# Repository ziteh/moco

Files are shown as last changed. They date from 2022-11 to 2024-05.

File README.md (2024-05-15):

# moco

|  SC1  | RD501 |
| :---: | :---: |
|  |  |

BLDC/PMSM motor controller/driver boards. [SC1 Demo video](https://youtu.be/PZ3AqAKdYeg)

- [SC1](/hardware/moco-sc1/): STSPIN32G4 + CSD88584Q5DC. Square PCB 40x40mm.
- [RD501](/hardware/moco-rd501/): DRV8301 + STM32G431. Square PCB 50x50mm.
- [RD321](/hardware/moco-rd321/): STSPIN32F0A + SiZ250DT. Square PCB 32x32mm.
- [OD501](/hardware/moco-od501/): DRV8323H + STM32G431. Round PCB Ø50mm.
- [OI401](/hardware/moco-oi401/): DRV8316C + STM32G431. Round PCB Ø40mm.
- [PG4](/hardware/moco-pg4/):  :construction: WIP.
- [BKD8316](/hardware/moco-bkd8316/): DRV8316 Breakout board

## Disclaimer & License

> [!WARNING]  
> None of the boards here are guaranteed to work.

These files are provided AS IS, without warranty of any kind.  
Including but not limited to manufacturing, assembly, procurement and use at your own risk.  
It is recommended to check yourself before use.  

For the full statement, please see license.  
Hardware licensed under the [CERN-OHL-P v2](/LICENSE-CERN-OHL-P), firmware licensed under the [MIT License](/LICENSE-MIT).

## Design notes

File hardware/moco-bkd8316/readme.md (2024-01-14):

# moco-bkd8316

- [DRV8316](https://www.ti.com/product/DRV8316) 40V max 8A peak, gate driver + FETs power stage + current sensing.

## PCB

### Board Characteristics

- Copper layer count: 2
- Board overall dimensions: 35.5 x 41 mm
- Min track/spacing: 0.2 mm / 0.2 mm
- Min hole diameter: 0.3 mm
- Castellated pads: No
- Edge card connectors: No
- Plated board edge: No

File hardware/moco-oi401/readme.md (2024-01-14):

# moco-OI401

- 10V~35V operating voltage
- 8A peak current
- 3x or 6xPWM control
- 3-Phase low-side current sense
- Ø40mm round PCB
- 3xM2 mounting holes, P.C.D Ø35.5mm
- [STM32G431CBU6](https://www.st.com/en/microcontrollers-microprocessors/stm32g431cb.html) 170 MHz MCU
- [DRV8316C](https://www.ti.com/product/DRV8316C) gate driver integrated FETs
- AS5047x magnetic encoder

## Pinmap

| Description | DRV8316 | STM32 | STM32 Func |
| --- | --- | ----- | --- |
| PWM-A High | INHA | PA10  | TIM1_CH3 |
| PWM-B High | INHB | PA9 | TIM1_CH2 |
| PWM-C High | INHC | PA8 | TIM1_CH1 |
| PWM-A Low | INLA | PC15  | TIM1_CH3N  |
| PWM-B Low | INLB | PA12  | TIM1_CH2N  |
| PWM-C Low | INLC | PB13  | TIM1_CH1N  |
| Current sense A | SOA | PA5 | ADC2_IN13  |
| Current sense B | SOB | PA6 | ADC2_IN3 |
| Current sense C | SOC | PA7 | ADC2_IN4 |
| nEnable | DRVOFF  | PB12  | |
| nFAULT | nFAULT  | PB11  | |
| SPI SCLK | SCLK | PB3 | SPI1 |
| SPI MISO | SDI | PB4 | SPI1 |
| SPI MOSI | SDO | PB5 | SPI1 |
| SPI nCS DRV8316 | nSCS | PB9 | |
| SPI nCS AS5047x | -- | PB2 | |
| USART Tx | -- | PA2 | USART2 |
| USART Rx | -- | PA3 | USART2 |
| User LED 1 (Red) | -- | PA0 | Active LOW |
| User LED 2 (Blue) | -- | PA1 | Active LOW |
| 5V indicator LED (Green) | -- | -- | |

## Jumper
- SB1 (3.3V LDO Bypass)
  - ON: 3.3V LDO bypassed, 3.3V provided through the buck regulator of DRV8316.
  - OFF (Default): 3.3V provided through the LDO.
- SB2 (nSLEEP Reset)
  - ON: Connected DRV8316 `nSLEEP` pin to RESET button.
  - OFF (Default): Disconnected DRV8316 `nSLEEP` pin to RESET button.
- SB3 (Voltage Reference Selection)
  - ON (Default): Connected +3.3V to STM32 `VREF+` and DRV8316 `VREF/LILM`, `VREF+` used as input.
  - OFF: Disconnected +3.3V to STM32 `VREF+` and DRV8316 `VREF/LILM`, voltage reference powered by STM32G4 embed voltage reference buffer, `VREF+` used as output.

## SPI

- Mode=1
  - CPOL=0. Clock is low when idle.
  - CPHA=1. Data sampled on 2nd edge (i.e. falling edge).
- 16-bit data frame.
- MSB first.
- nCS pin active low.
- 5MHz clock (limited by DRV8316).

## Board Characteristics

- Copper layer count: 2
- Board overall dimensions: 40 x 40 mm
- Min track/spacing: 0.13 mm / 0.13 mm
- Min hole diameter: 0.3 mm
- Castellated pads: No
- Edge card connectors: No
- Plated board edge: No

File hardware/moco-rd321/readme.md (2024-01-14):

# moco-RD321

- 6.7V~35V, 12A
- 3-Phase low-side current sensing. OP-Amp Gain=6.74, Shunt resistor=20mΩ
- Overcurrent detection. Ith=30A @ OC_COMPth=500mV
- Input voltage sensing
- 32x32mm square PCB, 4xM2 mounting holes
- [STSPIN32F0A](https://www.st.com/en/motor-drivers/stspin32f0a.html) 3-phase gate driver with embdded MCU SiP
  - STM32F031C6 48MHz, 4KB SRAM, 32KB Flash
  - 600mA sink/source gate drivers, integrated bootstrap diodes
  - 12V LDO and 3.3V buck
- [SiZ250DT](https://www.vishay.com/en/product/77227/) Dual N-MOSFET, 60V, 38A, 3.3x3.3mm
- MA702 magnetic encoder, SPI
- 2x04 2.54mm Pin header for debug, JST SM03B-SRSS-TB 1x03 for Serial and I2C

## Pinmap

| Description | Analog IC | STM32 | STM32 Func |
| --- | --- | ----- | --- |
| High-side U | HS1 | PA8 | TIM1_CH1 |
| High-side V | HS2 | PA9 | TIM1_CH2 |
| High-side W | HS3 | PA10  | TIM1_CH3 |
| Low-side U | LS1 | PB13  | TIM1_CH1N |
| Low-side V | LS2 | PB14  | TIM1_CH2N |
| Low-side W | LS3 | PB15  | TIM1_CH3N |
| OC threshold select 1 | OC_TH_STBY1  | PF7 | Push-pull output |
| OC threshold select 2 | OC_TH_STBY2  | PF6 | Push-pull output |
| OC protection selection  | OC_SEL | PA11  | Push-pull output |
| OC comparator output | OC_COMP_INT  | PB12  | TIM1_BKIN |
| OC comparator output | OC_COMP_INT2 | PA12  | TIM1_ETR |
| Current sense U | OP3O | PA0 | ADC_IN0 |
| Current sense V | OP2O | PA1 | ADC_IN1 |
| Current sense W | OP1O | PB1 | ADC_IN9 |
| VM sense | -- | PA4 | ADC_IN4 |
| SPI SCLK | -- | PA5 | SPI1 |
| SPI MISO | -- | PA6 | SPI1 |
| SPI MOSI | -- | PA7 | SPI1 |
| SPI nCS MA702 | -- | PA15  | |
| USART Tx | -- | PA2 | USART1 |
| USART Rx | -- | PA3 | USART1 |
| I2C SCL | -- | PB6 | I2C1 |
| I2C SDA | -- | PB7 | I2C1 |
| SWDIO | -- | PA13  | |
| SWCLK | -- | PA14  | |
| Connected to GND | -- | BOOT0 | |
| User LED (Red) | -- | PF0 | Active HIGH |
| 12V indicator LED (Blue) | -- | -- | |

> - Unused GPIOs inside the package should be config to output low: PB0, PB2, PB3, PB4, PB5, PB8, PB9, PB10, PB11, PC13, PC14, PC15.
> - OC_TH_STBY1 and OC_TH_STBY2 should be HIGH for 500mV OC threshold.
> - For analog IC, the GPIO input config without pull-up or -down is always allowed.

## PCB

### Jumper

If input voltage (i.e. VM)<15V then close `SB1` to connect VM pin and VREG12 pin.

### Board Characteristics

- Copper layer count: 4
- Board overall dimensions: 32 x 32 mm
- Min track/spacing: 0.13 mm / 0.13 mm
- Min hole diameter: 0.3 mm
- Castellated pads: No
- Edge card connectors: No
- Plated board edge: No
- 1oz copper

## SPI

MA702 encoder SPI:
- Mode:
  - 0 (CPOL=0, CPHA=0) or 1 (CPOL=1, CPHA=1)
  - Data sampled on first edge
- 16-bit data frame
- MSB first
- nCS pin active low
- 25MHz clock

## MCU

| STSPIN32*x* | [F0](https://www.st.com/en/motor-drivers/stspin32f0.html) | [F0***A***](https://www.st.com/en/motor-drivers/stspin32f0a.html) | [F0***B***](https://www.st.com/en/motor-drivers/stspin32f0b.html) |
| --- | --- | --- | --- |
| Operating voltage | 8~45V | 6.7~45V | 6.7~45V |
| OP-Amps | 4 | 3 | 1 |
| GPIOs | 15 | 16 | 20 |
| BOOT0 pin | -- | Yes | Yes |
| 3FG decoding logic for Hall sensors | Yes | -- | -- |
| Comparator | OCP | OCP and current control | OCP and current control |
| Package | QFN 7x7mm 1EP | QFN 7x7mm 1EP | QFN 7x7mm 1EP |

> [Solved: STSPIN32F0 vs STSPIN32F0A vs STSPIN32F0B - STMicroelectronics Community](https://community.st.com/t5/power-management/stspin32f0-vs-stspin32f0a-vs-stspin32f0b/td-p/273388)

## Reference

- [qwertpas/O32controller: Miniature closed-loop controller for brushless DC motors](https://github.com/qwertpas/O32controller)
- [STspin32G4 support - hardware support - SimpleFOC Community](https://community.simplefoc.com/t/stspin32g4-support/2027/6?page=3)
- ST AN5397 *"Current Sensing in motion control applications"*
- ST AN4999 *"STSPIN32F0/F0A/F0B overcurrent protection"*
- ST DB3364 *"STEVAL-SPIN3202: STSPIN32F0A advanced 3-phase BLDC driver with embedded STM32 MCU single shunt evaluation board"*
- ST DB4049 *"EVALKIT-ROBOT-1: Compact reference design kit for robotics and automation based on STSPIN32F0A"*
- ST DB3798 *"STEVAL-ESC002V1: Electronic Speed Controller reference design based on STSPIN32F0A"*
- TI SLUA887 *"Bootstrap Circuitry Selection for Half-Bridge Configurations"*
- Diodes DN1156 *"Gate Drivers in BLDC Motors"*

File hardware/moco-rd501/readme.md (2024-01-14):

# moco-RD501



STM32G431C8T6 MCU, DRV8301 gate driver, CSD18540Q5B power N-MOSFETs and AS5047x magnetic encoder.

Based on [ODrive](https://github.com/odriverobotics/ODriveHardware) `v3.5` PCB and [SimpleFOC](https://simplefoc.com/) firmware.

> Seems unstable.

| Front | Back | Layers |
| --- | --- | --- |
|  |  |  |

### Pinmap

| Description | STM32 Pin |
| --- | --- |
| PWM-A High | PA8 |
| PWM-B High | PA9 |
| PWM-C High | PA10 |
| PWM-A Low | PC13 |
| PWM-B Low | PA12 |
| PWM-C Low | PB15 |
| EN_Gate (Enable) | PB3 |
| nFAULT | PB10 |
| Encoder A | PB5 |
| Encoder B | PB6 |
| Encoder I | PB4 |
| SPI SCLK | PA5 |
| SPI MISO | PA6 |
| SPI MOSI | PA7 |
| SPI nCS DRV8301 | PB13 |
| SPI nCS AS5047x | PB14 |
| SPI nCS CAN-Bus | PB9 |
| CAN-Bus INT | PA11 |
| USART Tx | PA2 |
| USART Rx | PA3 |
| I2C SCL | PA15 |
| I2C SDA | PB7 |
| Current sense 1 (CH-B) | PA0 |
| Current sense 2 (CH-C) | PA1 |
| Temperature sense | PA4 |
| V_drive sense | PB12 |
| User LED 1 (Red) | PB0 |
| User LED 2 (Blue) | PB1 |
| GPIO PB2 | PB2 |
| GPIO PB11 | PB11 |

### Board Characteristics

- Copper layer count: 4
- Board overall dimensions: 50 x 50 mm
- Min track/spacing: 0.2 mm / 0.2 mm
- Min hole diameter: 0.2 mm
- Castellated pads: No
- Edge card connectors: No
- Plated board edge: No

Support JLCPCB's PCBA service.

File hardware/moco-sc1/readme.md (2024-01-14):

# moco-SC1

- 10V~35V, 12A
- 3-Phase low-side current sensing. Op-amp Gain=6.74, shunt resistor=20mΩ
- Input voltage sensing
- 40x40mm square PCB, 4xM3 mounting holes.
- [STSPIN32G4](https://www.st.com/en/motor-drivers/stspin32g4.html) 3-phase gate driver with embdded MCU SiP
  - [STM32G431VBx3](https://www.st.com/en/microcontrollers-microprocessors/stm32g431vb.html) 170MHz, 32KB SRAM, 128KB Flash
  - 1A sink/source gate drivers, integrated bootstrap diodes
  - 8~15V/200mA programmable buck for gate driver and 3.3V/150mA LDO
- [CSD88584Q5DC](https://www.ti.com/product/CSD88584Q5DC) Dual N-MOSFET half-bridge, 40V, 50A, 5x6mm
- [MA702](https://www.monolithicpower.com/en/ma702.html) magnetic encoder, SPI interface
- [TCAN33x](https://www.ti.com/product/TCAN330) 3.3V CAN transceiver
- 2x04 2.54mm Pin header for debug, JST GH 1.25mm 1x03 for CAN bus

## PCB

PCB online preview available [here](https://kicanvas.org/?github=https%3A%2F%2Fgithub.com%2Fziteh%2Fmoco%2Ftree%2Fmain%2Fhardware%2Fmoco-sc1), powered by [KiCanvas](https://github.com/theacodes/kicanvas).

### Jumper

`SB1`: Close to connect CAN bus 120Ω terminal resistor.

### Board Characteristics

- Copper layer count: 4
- Board overall dimensions: 40 x 40 mm
- Min track/spacing: 0.2 mm / 0.2 mm
- Min hole diameter: 0.3 mm
- Castellated pads: No
- Edge card connectors: No
- Plated board edge: No
- 1 or 2oz copper available

## SPI

MA702 encoder SPI:
- Mode:
  - 0 (CPOL=0, CPHA=0) or 3 (CPOL=1, CPHA=1) detected automatically
  - Data sampled on rising edge, transmission on falling
- 16-bit data frame
- MSB first
- nCS pin active low
- 25MHz clock max

## Pinmap

| Description | Gate Driver | STM32 | STM32 Func |
| --- | --- | ----- | --- |
| High-side A | INH1 | PE9 | TIM1_CH1 |
| High-side B | INH2 | PE11  | TIM1_CH2 |
| High-side C | INH3 | PE13  | TIM1_CH3 |
| Low-side A | INL1 | PE8 | TIM1_CH1N |
| Low-side B | INL2 | PE10  | TIM1_CH2N |
| Low-side C | INL3 | PE12  | TIM1_CH3N |
| Active high for wakeup | WAKE | PE7 | Push-pull output |
| Device ready signal | READY | PE14  | TIM1_BKIN2, pull-up input |
| Fault signal | NFAULT | PE15  | TIM1_BKIN, pull-up input  |
| | SCL | PC8 | I2C3 |
| | SDA | PC9 | I2C3 |
| Enable short-circuit protection | SCREF | -- | |
| Current sense Op-amp In+ A | -- | PA1 | OPAMP1_VINP |
| Current sense Op-amp In- A | -- | PA3 | OPAMP1_VINM |
| Current sense Op-amp Out A | -- | PA2 | OPAMP1_VOUT, ADC1_IN3 |
| Current sense Op-amp In+ B | -- | PA7 | OPAMP2_VINP |
| Current sense Op-amp In- B | -- | PC5 | OPAMP2_VINM |
| Current sense Op-amp Out B | -- | PA6 | OPAMP2_VOUT, ADC2_IN3 |
| Current sense Op-amp In+ C | -- | PB0 | OPAMP3_VINP |
| Current sense Op-amp In- C | -- | PB2 | OPAMP3_VINM |
| Current sense Op-amp Out C | -- | PB1 | OPAMP3_VOUT, ADC1_IN12 |
| VBUS sense | -- | PA4 | ADC2_IN17 |
| SPI SCLK | -- | PB3 | SPI1/3 |
| SPI MISO | -- | PB4 | SPI1/3 |
| SPI MOSI | -- | PB5 | SPI1/3 |
| SPI nCS MA702 | -- | PB6 | |
| USART TX | -- | PA9 | USART1 |
| USART RX | -- | PA10  | USART1 |
| CAN TX | -- | PA12  | FDCAN1 |
| CAN RX | -- | PA11  | FDCAN1 |
| SWDIO | -- | PA13  | |
| SWCLK | -- | PA14  | |
| SWO | -- | PA15  | |
| HSE OSC | -- | PF0 | OSC_IN |
| HSE OSC | -- | PF1 | OSC_OUT |
| Reset | -- | PG10  | NRST |
| BOOT, connected to GND | -- | PB8 | BOOT0 |
| User LED (Red), active high | -- | PA0 | TIM2_CH1 |
| VCC indicator LED (Blue) | -- | -- | |

> - For gate driver internal connected GPIO, the input pin config without pull-up or -down is always allowed.
> - It is recommended to set PB8 (BOOT0) in a mode other than analog mode after startup to limit consumption.

## STSPIN32 SiP

| STSPIN32 | [F0][32f0] | [F0A][32f0a] | [F0B][32f0b] | [G4][32g4] |
| --- | --- | --- | --- | --- |
| MCU | STM32F031C6 | STM32F031C6 | STM32F031C6 | STM32G431VB |
| Clock | 48 MHz | 48 MHz | 48 MHz | 170 MHz |
| SRAM | 4 KB | 4 KB | 4 KB | 32 KB |
| Flash | 32 KB | 32 KB | 32 KB | 128 KB |
| Operating voltage | 8~45V | 6.7~45V | 6.7~45V | 5.5~75V |
| OP-Amps | 4 | 3 | 1 | 3 |
| GPIOs | 15 | 16 | 20 | 40 |
| CAN Bus | 0 | 0 | 0 | 1 (CAN-FD) |
| USB | 0 | 0 | 0 | 1 (USB 2.0 FS) |
| BOOT0 pin | -- | Yes | Yes | Yes |
| Package | QFN-48 7x7mm 1EP | QFN-48 7x7mm 1EP | QFN-48 7x7mm 1EP | QFN-64 9x9mm 1EP |

> [Solved: STSPIN32F0 vs STSPIN32F0A vs STSPIN32F0B - STMicroelectronics Community](https://community.st.com/t5/power-management/stspin32f0-vs-stspin32f0a-vs-stspin32f0b/td-p/273388)

[32f0]: https://www.st.com/en/motor-drivers/stspin32f0.html
[32f0a]: https://www.st.com/en/motor-drivers/stspin32f0a.html
[32f0b]: https://www.st.com/en/motor-drivers/stspin32f0b.html
[32g4]: https://www.st.com/en/motor-drivers/stspin32g4.html

## Reference

- [runger1101001/simplefoc_funqi_example: Sample firmware for STSPIN32G4 based BLDC driver](https://github.com/runger1101001/simplefoc_funqi_example)
- [qwertpas/O32controller: Miniature closed-loop controller for brushless DC motors](https://github.com/qwertpas/O32controller)
- [Juanduino/STSPIN32G4-FunQi-Stack: SimpleFoc Format Dev. for potential 8pin PWM stepper use w. 4th half-bridge (also 6pin PWM BLDC use w. extra FET driver for eg. brake-resistor)](https://github.com/Juanduino/STSPIN32G4-FunQi-Stack)
  - [STspin32G4 support - hardware support - SimpleFOC Community](https://community.simplefoc.com/t/stspin32g4-support/2027/6?page=3)
- [EVSPIN32G4 - STSPIN32G4 demonstration board for three-phase brushless motors - STMicroelectronics](https://www.st.com/en/evaluation-tools/evspin32g4.html)
- [TIDA-01516 reference design | TI.com](https://www.ti.com/tool/TIDA-01516)
- [TIDA-00774 reference design | TI.com](https://www.ti.com/tool/TIDA-00774)
- ST AN5397 *"Current Sensing in motion control applications"*
- TI SLUA887 *"Bootstrap Circuitry Selection for Half-Bridge Configurations"*
- Diodes DN1156 *"Gate Drivers in BLDC Motors"*

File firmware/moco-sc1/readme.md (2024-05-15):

# moco SC1 Firmware

Simple firmware for moco SC1.

Currently only open loop velocity control, with SVPWM (Space Vector Pulse Width Modulation) or SPWM (Sinusoidal Pulse Width Modulation).

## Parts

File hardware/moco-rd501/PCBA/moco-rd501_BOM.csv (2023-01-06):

Comment | Designator | Footprint | LCSC
82pF | C5 | C_0402_1005Metric | C107011
47uF/50V | C26 | CP_Elec_6.3x7.7 | C108053
15nF | C8 | C_0402_1005Metric | C114405
1k | R19,R8 | R_0402_1005Metric | C11702
NCP18XH103F03RB | TH1 | R_0603_1608Metric | C13564
16MHz | Y2 | Crystal_SMD_3225-4Pin_3.2x2.5mm | C13738
100nF/50V | C14,C16,C19,C22,C23,C24 | C_0603_1608Metric | C14663
100nF | C36,C39,C40,C41,C42,C44,C45,C46 | C_0402_1005Metric | C1525
22nF | C18 | C_0402_1005Metric | C1532
12pF | C37,C38 | C_0402_1005Metric | C1547
10uF | C2 | C_0402_1005Metric | C15525
22pF | C47,C48 | C_0402_1005Metric | C1555
2.2nF | C20,C21,C6,C7 | C_0603_1608Metric | C1604
MCP25625 | U4 | QFN-28-1EP_6x6mm_P0.65mm_EP4.25x4.25mm | C191253
2.2R | R13,R14,R25,R26,R28,R29 | R_0603_1608Metric | C22939
4.7uF | C3 | C_0402_1005Metric | C23733
120R | R30,R31,R37 | R_0402_1005Metric | C25079
22R | R16,R17 | R_0402_1005Metric | C25092
330R | R9 | R_0402_1005Metric | C25104
680R | R5,R7 | R_0402_1005Metric | C25130
10k | R18,R2,R20,R24,R35,R36,R38,R4,R6 | R_0402_1005Metric | C25744
18k | R23,R33 | R_0402_1005Metric | C25762
220k 1% | R22 | R_0402_1005Metric | C25767
47k | R15 | R_0402_1005Metric | C25792
3.3k | R10,R11,R12,R21,R34 | R_0402_1005Metric | C25890
4.7k | R1,R3 | R_0402_1005Metric | C25900
Conn_02x02_Top_Bottom | J6,J7 | JST_GH_SM03B-GHS-TB_1x03-1MP_P1.25mm_Horizontal | C2829252
Conn_01x06 | J1 | JST_GH_SM06B-GHS-TB_1x06-1MP_P1.25mm_Horizontal | C2829255
Conn_01x09 | J4 | JST_GH_SM09B-GHS-TB_1x09-1MP_P1.25mm_Horizontal | C2829258
4.7uF/50V | C11,C17 | C_1206_3216Metric | C29823
22uH/1.5A | L1 | L_Bourns-SRN8040_8x8.15mm | C354640
LED_BAGR | LD1 | RGB LED 1.6x1.6mm | C375569
0.5mΩ | R27,R32 | R_2512_6332Metric | C469426
AS5147 | U5 | TSSOP-14_4.4x5mm_P0.65mm | C481876
2.2uF/16V | C10,C33 | C_0402_1005Metric | C501836
2.2uF/50V | C15,C27,C9 | C_1206_3216Metric | C50254
SW_Push | SW1,SW2 | SW_SPST_CK_RS282G05A3 | C520860
270pF | C1,C4 | C_0402_1005Metric | C524551
1uF | C12,C13,C43 | C_0402_1005Metric | C52923
STM32G431CBT6 | U3 | LQFP-48_7x7mm_P0.5mm | C529355
8MHz | Y1 | Crystal_SMD_3225-4Pin_3.2x2.5mm | C57131
68uF | C25 | CP_EIA-6032-28_Kemet-C | C7220
CSD18540Q5B | Q1,Q2,Q3,Q4,Q5,Q6 | TDSON-8-1 | C86513
XC6220B331MR | U1 | SOT-23-5 | C86534
SS34 | D1 | D_SMA | C8678
Conn_01x02 | J3 | AMASS_XT60-M_1x02_P7.20mm_Vertical | C98733
DRV8301 | U2 | HTSSOP-56-1EP_6.1x14mm_P0.5mm_EP3.61x6.35mm | C98969
Debug | J2 | PinHeader_1x06_P2.54mm_Vertical
Conn_01x03 | J5 | AMASS MR30PB-F
100nF | C50 | C_0603_1608Metric
22uF/50V | C29 | C_1210_3225Metric_Pad1.33x2.70mm_HandSolder
1uF | C49 | C_0603_1608Metric
22uF/50V | C30 | C_1210_3225Metric_Pad1.33x2.70mm_HandSolder
22uF/50V | C31 | C_1210_3225Metric_Pad1.33x2.70mm_HandSolder
22uF/50V | C32 | C_1210_3225Metric_Pad1.33x2.70mm_HandSolder
22uF/50V | C28 | C_1210_3225Metric_Pad1.33x2.70mm_HandSolder
22uF/50V | C35 | C_1210_3225Metric_Pad1.33x2.70mm_HandSolder
22uF/50V | C34 | C_1210_3225Metric_Pad1.33x2.70mm_HandSolder

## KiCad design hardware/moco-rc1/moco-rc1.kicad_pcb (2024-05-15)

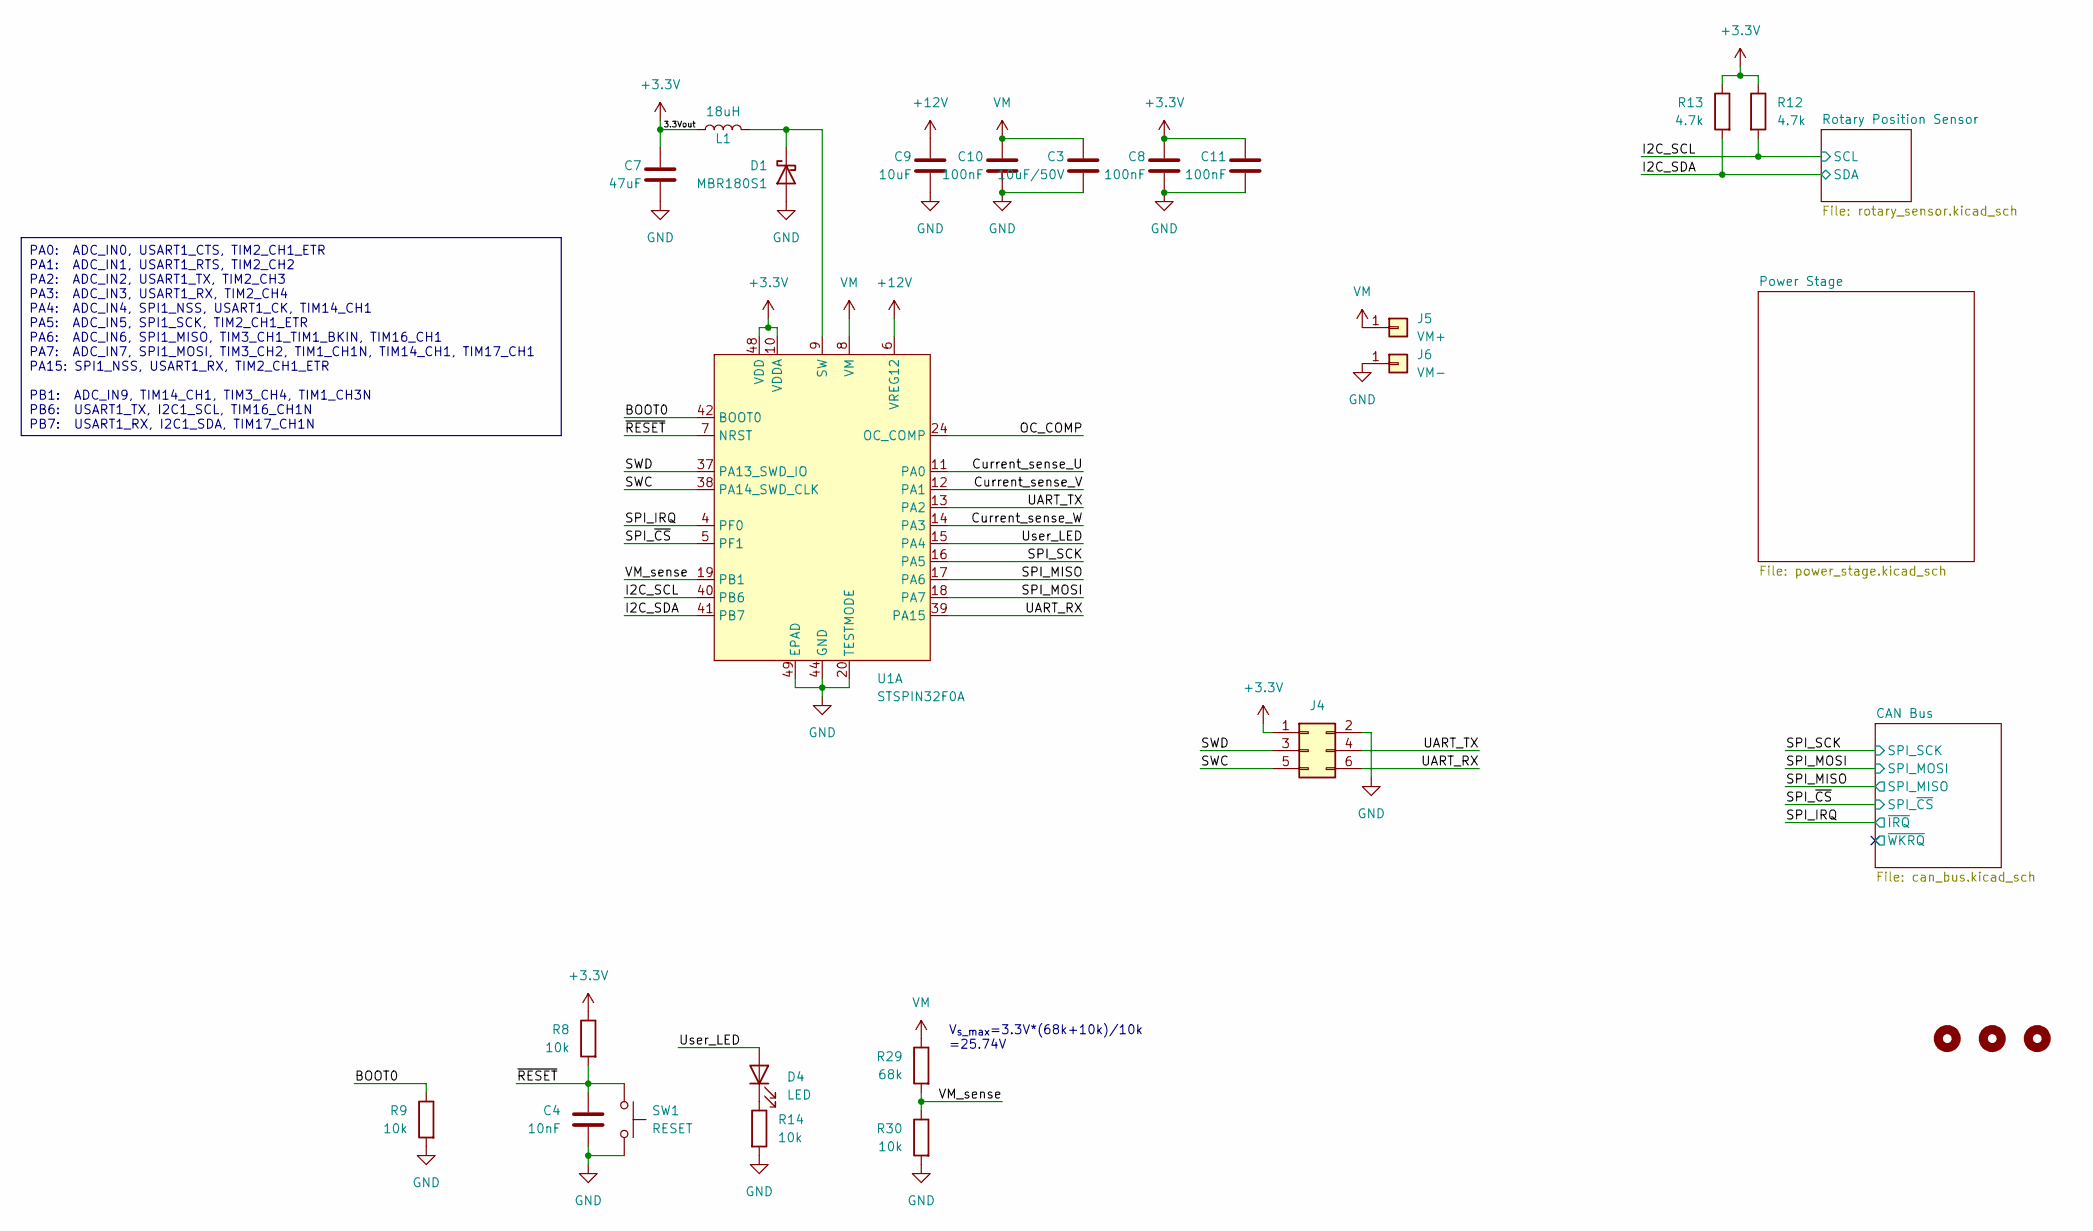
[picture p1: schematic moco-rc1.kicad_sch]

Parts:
C3: 10uF/50V; C_0805_2012Metric; MFR. Part# GRM21BR61H106KE43L; LCSC C440198
C4: 10nF; C_0402_1005Metric
C7: 47uF; C_0805_2012Metric; MFR. Part# GRM21BR61H106KE43L; LCSC C440198
C8, C10, C11: 100nF; C_0402_1005Metric; MFR. Part# GRM21BR61H106KE43L; LCSC C440198
C9: 10uF; C_0402_1005Metric; MFR. Part# GRM21BR61H106KE43L; LCSC C440198
D1: MBR180S1; D_SOD-123F; MFR. Part# MBR180S1-7; LCSC C526660
D4: LED; LED_0603_1608Metric
H1, H2, H3: MountingHole; MountingHole_2.2mm_M2_ISO7380
J4: Conn_02x03_Odd_Even; PinHeader_2x03_P2.54mm_Vertical
J5: VM+; Conn_1x1_3.7_1.5
J6: VM-; Conn_1x1_3.7_1.5
L1: 18uH; L_Neosid_SMS-ME3015; MFR. Part# FNR3012S180MT; LCSC C528020
R8, R9, R14, R30: 10k; R_0402_1005Metric
R12, R13: 4.7k; R_0402_1005Metric
R29: 68k; R_0402_1005Metric
SW1: RESET; SW_SPST_B3U-1000P
U1: STSPIN32F0A; VFQFN-48_7x7_EP2.8mm_Pitch0.5mm

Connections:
+3.3V: C7.1, C8.1, C11.1, J4.1, L1.1, R8.1, R12.1, R13.1, U1.10 (VDDA), U1.48 (VDD); also elsewhere on the board
+12V: C9.1, U1.6 (VREG12); also elsewhere on the board
/BOOT0: R9.1, U1.42 (BOOT0)
/Current_sense_U: U1.11 (PA0)
/Current_sense_V: U1.12 (PA1)
/Current_sense_W: U1.14 (PA3)
/I2C_SCL: R12.2, U1.40 (PB6); also elsewhere on the board
/I2C_SDA: R13.2, U1.41 (PB7); also elsewhere on the board
/OC_COMP: U1.24 (OC_COMP)
/SPI_IRQ: U1.4 (PF0); also elsewhere on the board
/SPI_MISO: U1.17 (PA6); also elsewhere on the board
/SPI_MOSI: U1.18 (PA7); also elsewhere on the board
/SPI_SCK: U1.16 (PA5); also elsewhere on the board
/SPI_~CS: U1.5 (PF1); also elsewhere on the board
/SWC: J4.5, U1.38 (PA14_SWD_CLK)
/SWD: J4.3, U1.37 (PA13_SWD_IO)
/UART_RX: J4.6, U1.39 (PA15)
/UART_TX: J4.4, U1.13 (PA2)
/User_LED: D4.2 (A), U1.15 (PA4)
/VM_sense: R29.2, R30.1, U1.19 (PB1)
/~RESET: C4.1, R8.2, SW1.1, U1.7 (NRST)
GND: C3.2, C4.2, C7.2, C8.2, C9.2, C10.2, C11.2, D1.2 (A), J4.2, J6.1, R9.2, R14.2, R30.2, SW1.2, U1.20 (TESTMODE), U1.44 (GND), U1.49 (EPAD); also elsewhere on the board
unnamed: D1.1 (K), L1.2, U1.9 (SW)
unnamed: D4.1 (K), R14.1
VM: C3.1, C10.1, J5.1, R29.1, U1.8 (VM); also elsewhere on the board

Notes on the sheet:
PA0: ADC_IN0, USART1_CTS, TIM2_CH1_ETR PA1: ADC_IN1, USART1_RTS, TIM2_CH2 PA2: ADC_IN2, USART1_TX, TIM2_CH3 PA3: ADC_IN3, USART1_RX, TIM2_CH4 PA4: ADC_IN4, SPI1_NSS, USART1_CK, TIM14_CH1 PA5: ADC_IN5, SPI1_SCK, TIM2_CH1_ETR PA6: ADC_IN6, SPI1_MISO, TIM3_CH1_TIM1_BKIN, TIM16_CH1 PA7: ADC_IN7, SPI1_M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
V_{s_max}=3.3V*(68k+10k)/10k =25.74V

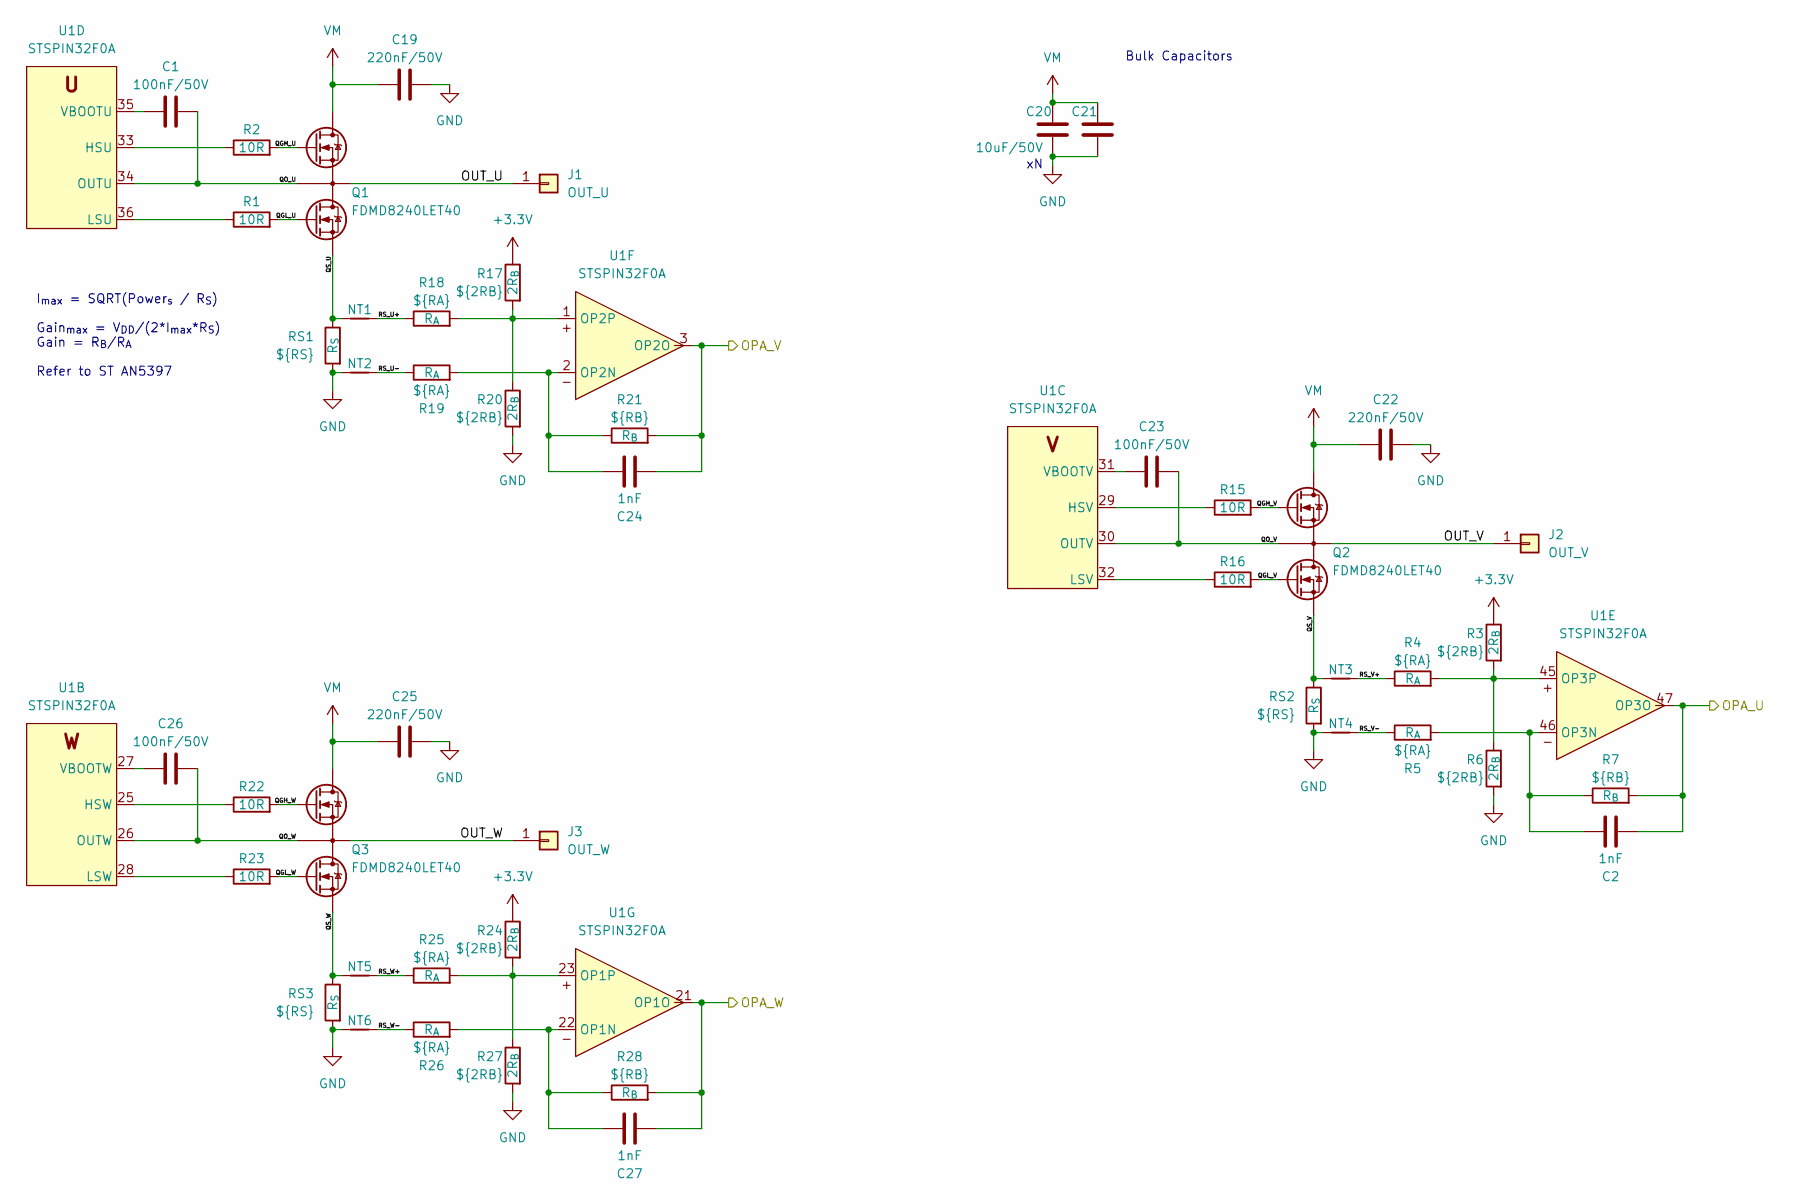
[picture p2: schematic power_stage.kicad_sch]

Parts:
C1, C23, C26: 100nF/50V; C_0402_1005Metric
C2, C24, C27: 1nF; C_0402_1005Metric
C19, C22, C25: 220nF/50V; C_0402_1005Metric
C20, C21: 10uF/50V; C_0805_2012Metric
J1: OUT_U; Conn_1x1_3.7_1.5
J2: OUT_V; Conn_1x1_3.7_1.5
J3: OUT_W; Conn_1x1_3.7_1.5
NT1, NT2, NT3, NT4, NT5, NT6: NetTie_2; NetTie-2_SMD_Pad0.5mm
Q1, Q2, Q3: FDMD8240LET40; PQFN-12
R1, R2, R15, R16, R22, R23: 10R; R_0402_1005Metric
R3, R6, R17, R20, R24, R27: ${2RB}; R_0402_1005Metric
R4, R5, R18, R19, R25, R26: ${RA}; R_0402_1005Metric
R7, R21, R28: ${RB}; R_0402_1005Metric
RS1, RS2, RS3: ${RS}; R_2512_6332Metric_Pad1.40x3.35mm_HandSolder
U1: STSPIN32F0A; VFQFN-48_7x7_EP2.8mm_Pitch0.5mm

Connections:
+3.3V: R3.1, R17.1, R24.1; also elsewhere on the board
/Power Stage/OPA_U: C2.1, R7.2, U1.47 (OP3O)
/Power Stage/OPA_V: C24.1, R21.2, U1.3 (OP2O)
/Power Stage/OPA_W: C27.1, R28.2, U1.21 (OP1O)
/Power Stage/OUT_U: J1.1, Q1.7 (D2/S1), Q1.8 (D2/S1), Q1.9 (D2/S1), Q1.10 (D2/S1), Q1.14 (D2/S1)
/Power Stage/OUT_V: J2.1, Q2.7 (D2/S1), Q2.8 (D2/S1), Q2.9 (D2/S1), Q2.10 (D2/S1), Q2.14 (D2/S1)
/Power Stage/OUT_W: J3.1, Q3.7 (D2/S1), Q3.8 (D2/S1), Q3.9 (D2/S1), Q3.10 (D2/S1), Q3.14 (D2/S1)
/Power Stage/QGH_U: Q1.12 (G1), R2.2
/Power Stage/QGH_V: Q2.12 (G1), R15.2
/Power Stage/QGH_W: Q3.12 (G1), R22.2
/Power Stage/QGL_U: Q1.4 (G2), R1.2
/Power Stage/QGL_V: Q2.4 (G2), R16.2
/Power Stage/QGL_W: Q3.4 (G2), R23.2
/Power Stage/QO_U: C1.2, Q1.11 (G1R), U1.34 (OUTU)
/Power Stage/QO_V: C23.2, Q2.11 (G1R), U1.30 (OUTV)
/Power Stage/QO_W: C26.2, Q3.11 (G1R), U1.26 (OUTW)
/Power Stage/QS_U: NT1.1, Q1.5 (S2), Q1.6 (S2), RS1.1
/Power Stage/QS_V: NT3.1, Q2.5 (S2), Q2.6 (S2), RS2.1
/Power Stage/QS_W: NT5.1, Q3.5 (S2), Q3.6 (S2), RS3.1
/Power Stage/RS_U+: NT1.2, R18.1
/Power Stage/RS_U-: NT2.2, R19.1
/Power Stage/RS_V+: NT3.2, R4.1
/Power Stage/RS_V-: NT4.2, R5.1
/Power Stage/RS_W+: NT5.2, R25.1
/Power Stage/RS_W-: NT6.2, R26.1
GND: C19.2, C20.2, C21.2, C22.2, C25.2, NT2.1, NT4.1, NT6.1, R6.2, R20.2, R27.2, RS1.2, RS2.2, RS3.2; also elsewhere on the board
unnamed: R22.1, U1.25 (HSW)
unnamed: R23.1, U1.28 (LSW)
unnamed: C26.1, U1.27 (VBOOTW)
unnamed: R15.1, U1.29 (HSV)
unnamed: R16.1, U1.32 (LSV)
unnamed: C23.1, U1.31 (VBOOTV)
unnamed: R2.1, U1.33 (HSU)
unnamed: R1.1, U1.36 (LSU)
unnamed: C1.1, U1.35 (VBOOTU)
unnamed: C2.2, R5.2, R7.1, U1.46 (OP3N)
unnamed: R3.2, R4.2, R6.1, U1.45 (OP3P)
unnamed: C24.2, R19.2, R21.1, U1.2 (OP2N)
unnamed: R17.2, R18.2, R20.1, U1.1 (OP2P)
unnamed: C27.2, R26.2, R28.1, U1.22 (OP1N)
unnamed: R24.2, R25.2, R27.1, U1.23 (OP1P)
VM: C19.1, C20.1, C21.1, C22.1, C25.1, Q1.1 (D1), Q1.2 (D1), Q1.3 (D1), Q1.13 (D1), Q2.1 (D1), Q2.2 (D1), Q2.3 (D1), Q2.13 (D1), Q3.1 (D1), Q3.2 (D1), Q3.3 (D1), Q3.13 (D1); also elsewhere on the board

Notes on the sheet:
I_{max} = SQRT(Power_{s} / R_{S}) Gain_{max} = V_{DD}/(2*I_{max}*R_{S}) Gain = R_{B}/R_{A} Refer to ST AN5397
Bulk Capacitors

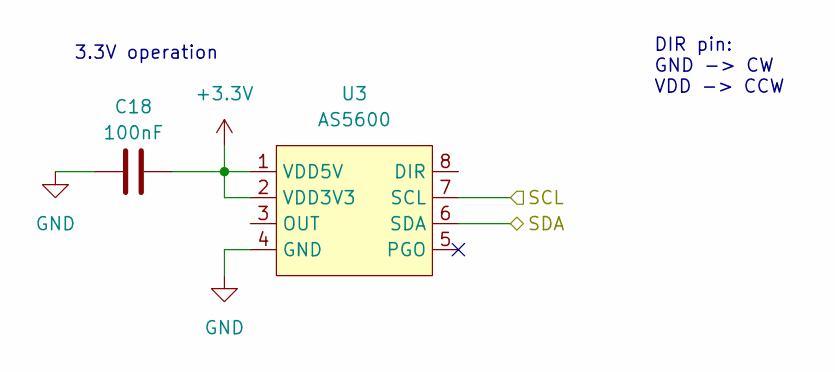
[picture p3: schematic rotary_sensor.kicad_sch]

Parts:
C18: 100nF; C_0603_1608Metric_Pad1.08x0.95mm_HandSolder
U3: AS5600; SOIC-8_3.9x4.9mm_P1.27mm

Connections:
+3.3V: C18.2, U3.1 (VDD5V), U3.2 (VDD3V3); also elsewhere on the board
/I2C_SCL: U3.7 (SCL); also elsewhere on the board
/I2C_SDA: U3.6 (SDA); also elsewhere on the board
GND: C18.1, U3.4 (GND); also elsewhere on the board

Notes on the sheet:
DIR pin: GND -> CW VDD -> CCW
3.3V operation

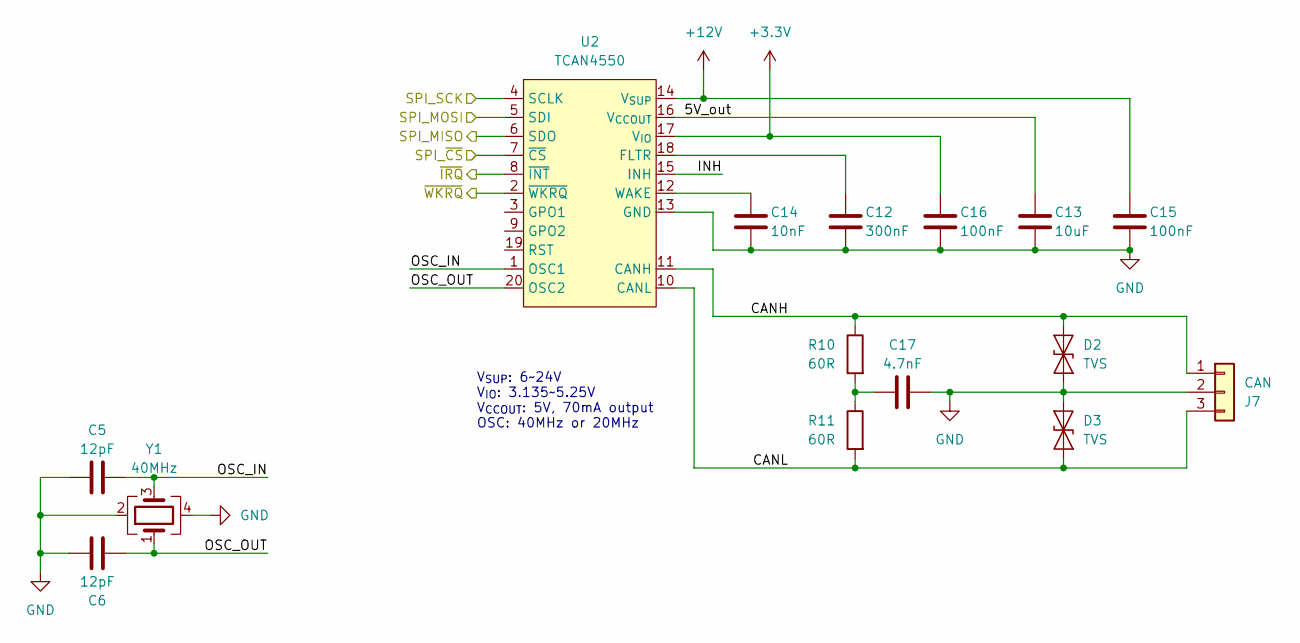
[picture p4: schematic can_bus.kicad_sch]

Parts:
C5, C6: 12pF; C_0402_1005Metric
C12: 300nF; C_0402_1005Metric
C13: 10uF; C_0402_1005Metric
C14: 10nF; C_0402_1005Metric
C15, C16: 100nF; C_0402_1005Metric
C17: 4.7nF; C_0402_1005Metric
D2, D3: TVS; D_SOD-323_HandSoldering
J7: CAN; JST_GH_SM03B-GHS-TB_1x03-1MP_P1.25mm_Horizontal
R10, R11: 60R; R_0402_1005Metric
U2: TCAN4550; VQFN-20_3.5_3.5_0.5p
Y1: 40MHz; Crystal_SMD_3225-4Pin_3.2x2.5mm

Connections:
+3.3V: C16.1, U2.17 (V_{IO}); also elsewhere on the board
+12V: C15.1, U2.14 (V_{SUP}); also elsewhere on the board
/CAN Bus/5V_out: C13.1, U2.16 (V_{CCOUT})
/CAN Bus/CANH: D2.2 (A2), J7.1, R10.1, U2.11 (CANH)
/CAN Bus/CANL: D3.1 (A1), J7.3, R11.2, U2.10 (CANL)
/CAN Bus/INH: U2.15 (INH)
/CAN Bus/OSC_IN: C5.2, U2.1 (OSC1), Y1.3
/CAN Bus/OSC_OUT: C6.1, U2.20 (OSC2), Y1.1
/CAN Bus/~WKRQ: U2.2 (~WKRQ)
/SPI_IRQ: U2.8 (~INT); also elsewhere on the board
/SPI_MISO: U2.6 (SDO); also elsewhere on the board
/SPI_MOSI: U2.5 (SDI); also elsewhere on the board
/SPI_SCK: U2.4 (SCLK); also elsewhere on the board
/SPI_~CS: U2.7 (~CS); also elsewhere on the board
GND: C5.1, C6.2, C12.2, C13.2, C14.2, C15.2, C16.2, C17.2, D2.1 (A1), D3.2 (A2), J7.2, U2.13 (GND), Y1.2, Y1.4; also elsewhere on the board
unnamed: C17.1, R10.2, R11.1
unnamed: C12.1, U2.18 (FLTR)
unnamed: C14.1, U2.12 (WAKE)

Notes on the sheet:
V_{SUP}: 6~24V V_{IO}: 3.135~5.25V V_{CCOUT}: 5V, 70mA output OSC: 40MHz or 20MHz

Board: 4 copper layers, 89 parts (13 on the bottom side), 68 nets, no tracks yet.

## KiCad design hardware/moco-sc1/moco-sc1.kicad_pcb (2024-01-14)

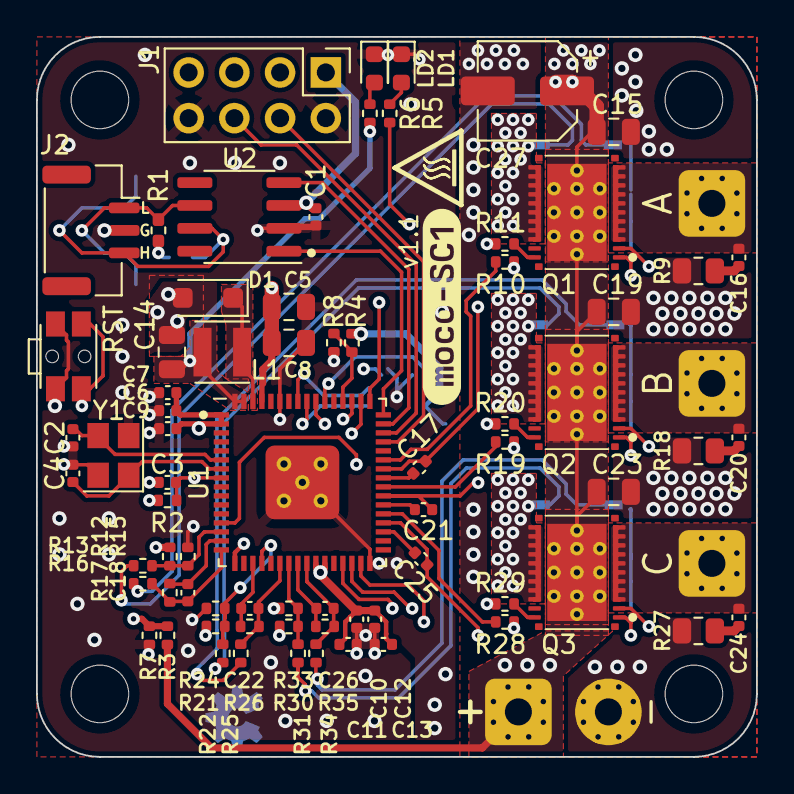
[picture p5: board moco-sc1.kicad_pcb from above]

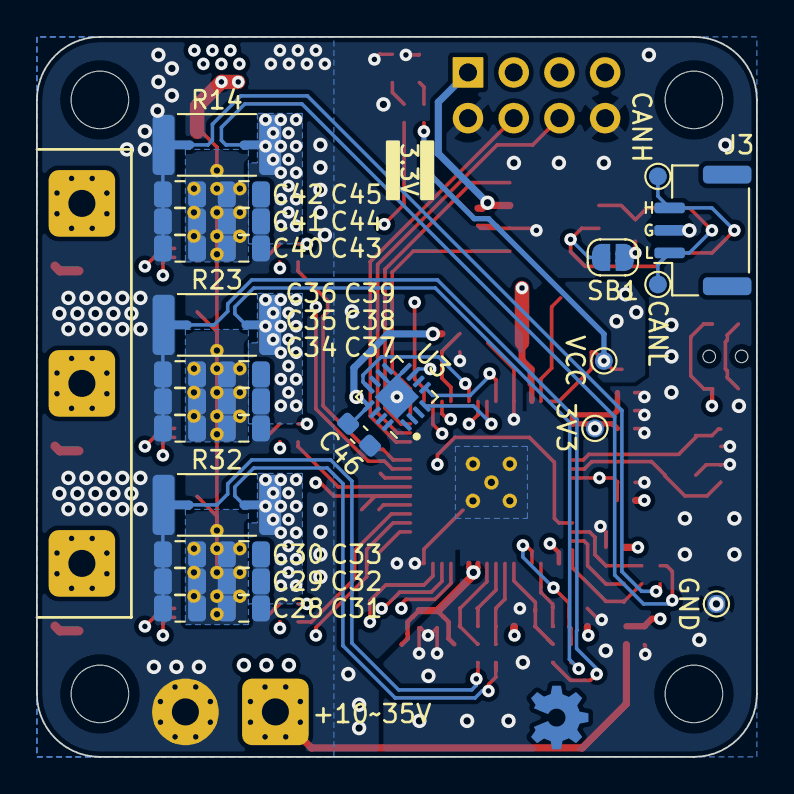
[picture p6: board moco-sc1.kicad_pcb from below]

Board: 4 copper layers, 40.0 x 40.0 mm, 118 parts (36 on the bottom side), 69 nets.

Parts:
C1, C3, C6, C9, C10, C12: 100nF; C_0402_1005Metric
C2, C4: 6.8pF; C_0402_1005Metric
C5, C28, C29, C30, C31, C32, C33, C34, C35, C36, C37, C38, C39, C40, C41, C42, C43, C44, C45: 10uF/50V; C_0805_2012Metric
C7: 10uF; C_0402_1005Metric
C8, C15, C19, C23: 220nF/50V; C_0805_2012Metric
C11, C13: 1uF; C_0402_1005Metric
C14: 10uF; C_0805_2012Metric
C16, C20, C24: 4.7nF/50V; C_0402_1005Metric
C17, C21, C25: 100nF/50V; C_0402_1005Metric
C18, C22, C26: 1nF; C_0402_1005Metric
C27: 22uF/50V; CP_Elec_5x5.8
C46: 1uF; C_0603_1608Metric_Pad1.08x0.95mm_HandSolder
D1: MBR180S1; D_SOD-123F
H1, H2, H3, H4: MountingHole; MountingHole_3.2mm_M3_ISO14580
J1: Debug; PinHeader_2x04_P2.54mm_Vertical
J2, J3: CAN; JST_GH_SM03B-GHS-TB_1x03-1MP_P1.25mm_Horizontal
J4: V+; wire_rectagnel_3.7mm_D1.5mm
J5: V-; wire_circ_3.7mm_D1.5mm
J6: A; wire_rectagnel_3.7mm_D1.5mm
J7: B; wire_rectagnel_3.7mm_D1.5mm
J8: C; wire_rectagnel_3.7mm_D1.5mm
L1: 18uH; L_Neosid_SMS-ME3015
LD1: Red; LED_0603_1608Metric
LD2: Blue; LED_0603_1608Metric
NT1, NT2, NT3, NT4, NT5, NT6: NetTie_2; NetTie-2_SMD_Pad0.5mm
Q1, Q2, Q3: CSD88584Q5DC; VSON-CLIP-22_5x6mm (DMM0022A)_Alt1
R1: 120R; R_0402_1005Metric_Pad0.72x0.64mm_HandSolder
R2, R6, R7, R8: 10k; R_0402_1005Metric
R3: 100k; R_0402_1005Metric
R4: 22k; R_0402_1005Metric
R5: 1k; R_0402_1005Metric
R9, R18, R27: 2.2R/125mW; R_0805_2012Metric
R10, R11, R19, R20, R28, R29: 10R; R_0402_1005Metric
R12, R15, R21, R24, R30, R33: 24k; R_0402_1005Metric
R13, R16, R22, R25, R31, R34: 1.78k; R_0402_1005Metric
R14, R23, R32: 20mΩ/3W; R_2512_6332Metric
R17, R26, R35: 12k; R_0402_1005Metric
SB1: SolderJumper_2_Open; SolderJumper-2_P1.3mm_Open_RoundedPad1.0x1.5mm
SW1: RESET; SW_SPST_EVQP7C
TP1: CANH; TestPoint_Pad_D1.0mm
TP2: CANL; TestPoint_Pad_D1.0mm
TP3: 3.3V; TestPoint_Pad_D1.0mm
TP4: VCC; TestPoint_Pad_D1.0mm
TP5: GND; TestPoint_Pad_D1.0mm
U1: STSPIN32G4; VFQFPN 9X9X1.0 64 PITCH 0.5
U2: TCAN337; SOIC-8_3.9x4.9mm_P1.27mm
U3: MA702; QFN-16-1EP_3x3mm_P0.5mm_EP1.75x1.75mm
Y1: 16MHz; Crystal_SMD_3225-4Pin_3.2x2.5mm
kibuzzard-64C58EFF: G***; kibuzzard-64C58EFF

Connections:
+3.3V: C1.2, C6.2, C7.2, C9.2, C10.2, C11.2, C12.2, C13.2, C46.2, J1.1, R2.2, R4.1, R12.1, R21.1, R30.1, TP3.1, U1.1 (REG3V3/VDD), U1.2 (VBAT), U1.26 (VREF+), U1.27 (VDDA), U2.3 (VCC), U3.13 (VDD)
/CANH: J2.3, J3.3, SB1.1 (A), TP1.1, U2.7 (CANH)
/CANL: J2.1, J3.1, R1.2, TP2.1, U2.6 (CANL)
/CAN_RX: U1.47 (PA11), U2.4 (RXD)
/CAN_TX: U1.48 (PA12), U2.1 (TXD)
/OPAMP1_VINM: C18.2, R16.2, R17.1, U1.16 (PA3)
/OPAMP1_VINP: R12.2, R13.2, R15.1, U1.14 (PA1)
/OPAMP1_VOUT: C18.1, R17.2, U1.15 (PA2)
/OPAMP2_VINM: C22.2, R25.2, R26.1, U1.22 (PC5)
/OPAMP2_VINP: R21.2, R22.2, R24.1, U1.20 (PA7)
/OPAMP2_VOUT: C22.1, R26.2, U1.19 (PA6)
/OPAMP3_VINM: C26.2, R34.2, R35.1, U1.25 (PB2)
/OPAMP3_VINP: R30.2, R31.2, R33.1, U1.23 (PB0)
/OPAMP3_VOUT: C26.1, R35.2, U1.24 (PB1)
/OSC_IN: C2.2, U1.6 (PF0), Y1.3
/OSC_OUT: C4.2, U1.7 (PF1), Y1.1
/Power Stage/OUTA: C16.1, J6.1, Q1.3 (VSW), Q1.4 (VSW), Q1.5 (VSW), Q1.6 (VSW), Q1.7 (VSW), Q1.8 (VSW), Q1.9 (VSW), Q1.10 (VSW), Q1.11 (VSW)
/Power Stage/OUTB: C20.1, J7.1, Q2.3 (VSW), Q2.4 (VSW), Q2.5 (VSW), Q2.6 (VSW), Q2.7 (VSW), Q2.8 (VSW), Q2.9 (VSW), Q2.10 (VSW), Q2.11 (VSW)
/Power Stage/OUTC: C24.1, J8.1, Q3.3 (VSW), Q3.4 (VSW), Q3.5 (VSW), Q3.6 (VSW), Q3.7 (VSW), Q3.8 (VSW), Q3.9 (VSW), Q3.10 (VSW), Q3.11 (VSW)
/Power Stage/RSA+: NT1.1, R13.1
/Power Stage/RSA-: NT2.1, R16.1
/Power Stage/RSB+: NT3.1, R22.1
/Power Stage/RSB-: NT4.1, R25.1
/Power Stage/RSC+: NT5.1, R31.1
/Power Stage/RSC-: NT6.1, R34.1
/Power Stage/S2A: NT1.2, Q1.12 (PGND), Q1.13 (PGND), Q1.14 (PGND), Q1.15 (PGND), Q1.16 (PGND), Q1.17 (PGND), Q1.18 (PGND), Q1.19 (PGND), Q1.20 (PGND), R14.1
/Power Stage/S2B: NT3.2, Q2.12 (PGND), Q2.13 (PGND), Q2.14 (PGND), Q2.15 (PGND), Q2.16 (PGND), Q2.17 (PGND), Q2.18 (PGND), Q2.19 (PGND), Q2.20 (PGND), R23.1
/Power Stage/S2C: NT5.2, Q3.12 (PGND), Q3.13 (PGND), Q3.14 (PGND), Q3.15 (PGND), Q3.16 (PGND), Q3.17 (PGND), Q3.18 (PGND), Q3.19 (PGND), Q3.20 (PGND), R32.1
/SCREF: R4.2, R8.1, U1.52 (SCREF)
/SPI_MISO: U1.55 (PB4), U3.7 (MISO)
/SPI_MOSI: U1.56 (PB5), U3.4 (MOSI)
/SPI_SCLK: U1.54 (PB3), U3.12 (SCLK)
/SPI_~CS_RS: U1.57 (PB6), U3.5 (~CS)
/SWCLK: J1.5, U1.50 (PA14)
/SWDIO: J1.3, U1.49 (PA13)
/SWO: J1.7, U1.51 (PA15)
/USART_RX: J1.6, U1.46 (PA10)
/USART_TX: J1.4, U1.45 (PA9)
/USER_LED: R5.1, U1.13 (PA0)
/V_{BUS}_SENSE: R3.1, R7.2, U1.17 (PA4)
/~RESET: C3.1, R2.1, SW1.1, U1.8 (PG10)
GND: C1.1, C2.1, C3.2, C4.1, C5.2, C6.1, C7.1, C8.2, C9.1, C10.1, C11.1, C12.1, C13.1, C14.2, C15.1, C19.1, C23.1, C27.2, C28.2, C29.2, C30.2, C31.2, C32.2, C33.2, C34.2, C35.2, C36.2, C37.2, C38.2, C39.2, C40.2, C41.2, C42.2, C43.2, C44.2, C45.2, C46.1, D1.2 (A), J1.2, J1.8, J2.2, J3.2, J5.1, LD1.1 (K), LD2.1 (K), NT2.2, NT4.2, NT6.2, R7.1, R8.2, R9.2, R14.2, R15.2, R18.2, R23.2, R24.2, R27.2, R32.2, R33.2, SW1.2, TP5.1, U1.32 (PGND), U1.59 (PB8), U1.65 (VSS), U2.2 (GND), U3.8 (GND), U3.10 (TEST), U3.17 (PAD), Y1.2, Y1.4
unnamed: C16.2, R9.1
unnamed: C20.2, R18.1
unnamed: C24.2, R27.1
unnamed: D1.1 (K), L1.1, U1.62 (SW)
unnamed: LD1.2 (A), R5.2
unnamed: LD2.2 (A), R6.2
unnamed: Q1.1 (GH), R10.2
unnamed: Q1.22 (GL), R11.2
unnamed: C17.1, Q1.2 (SH), U1.42 (OUT1)
unnamed: Q2.1 (GH), R19.2
unnamed: Q2.22 (GL), R20.2
unnamed: C21.1, Q2.2 (SH), U1.39 (OUT2)
unnamed: Q3.1 (GH), R28.2
unnamed: Q3.22 (GL), R29.2
unnamed: C25.1, Q3.2 (SH), U1.36 (OUT3)
unnamed: R1.1, SB1.2 (B)
unnamed: C17.2, U1.41 (BOOT1)
unnamed: R10.1, U1.43 (GHS1)
unnamed: R11.1, U1.29 (GLS1)
unnamed: C21.2, U1.38 (BOOT2)
unnamed: R19.1, U1.40 (GHS2)
unnamed: R20.1, U1.30 (GLS2)
unnamed: C25.2, U1.35 (BOOT3)
unnamed: R28.1, U1.37 (GHS3)
unnamed: R29.1, U1.31 (GLS3)
VBUS: C5.1, C8.1, C15.2, C19.2, C23.2, C27.1, C28.1, C29.1, C30.1, C31.1, C32.1, C33.1, C34.1, C35.1, C36.1, C37.1, C38.1, C39.1, C40.1, C41.1, C42.1, C43.1, C44.1, C45.1, J4.1, Q1.27 (VIN), Q2.27 (VIN), Q3.27 (VIN), R3.2, U1.61 (VM)
VCC: C14.1, L1.2, R6.1, TP4.1, U1.63 (VCC), U1.64 (REGIN)

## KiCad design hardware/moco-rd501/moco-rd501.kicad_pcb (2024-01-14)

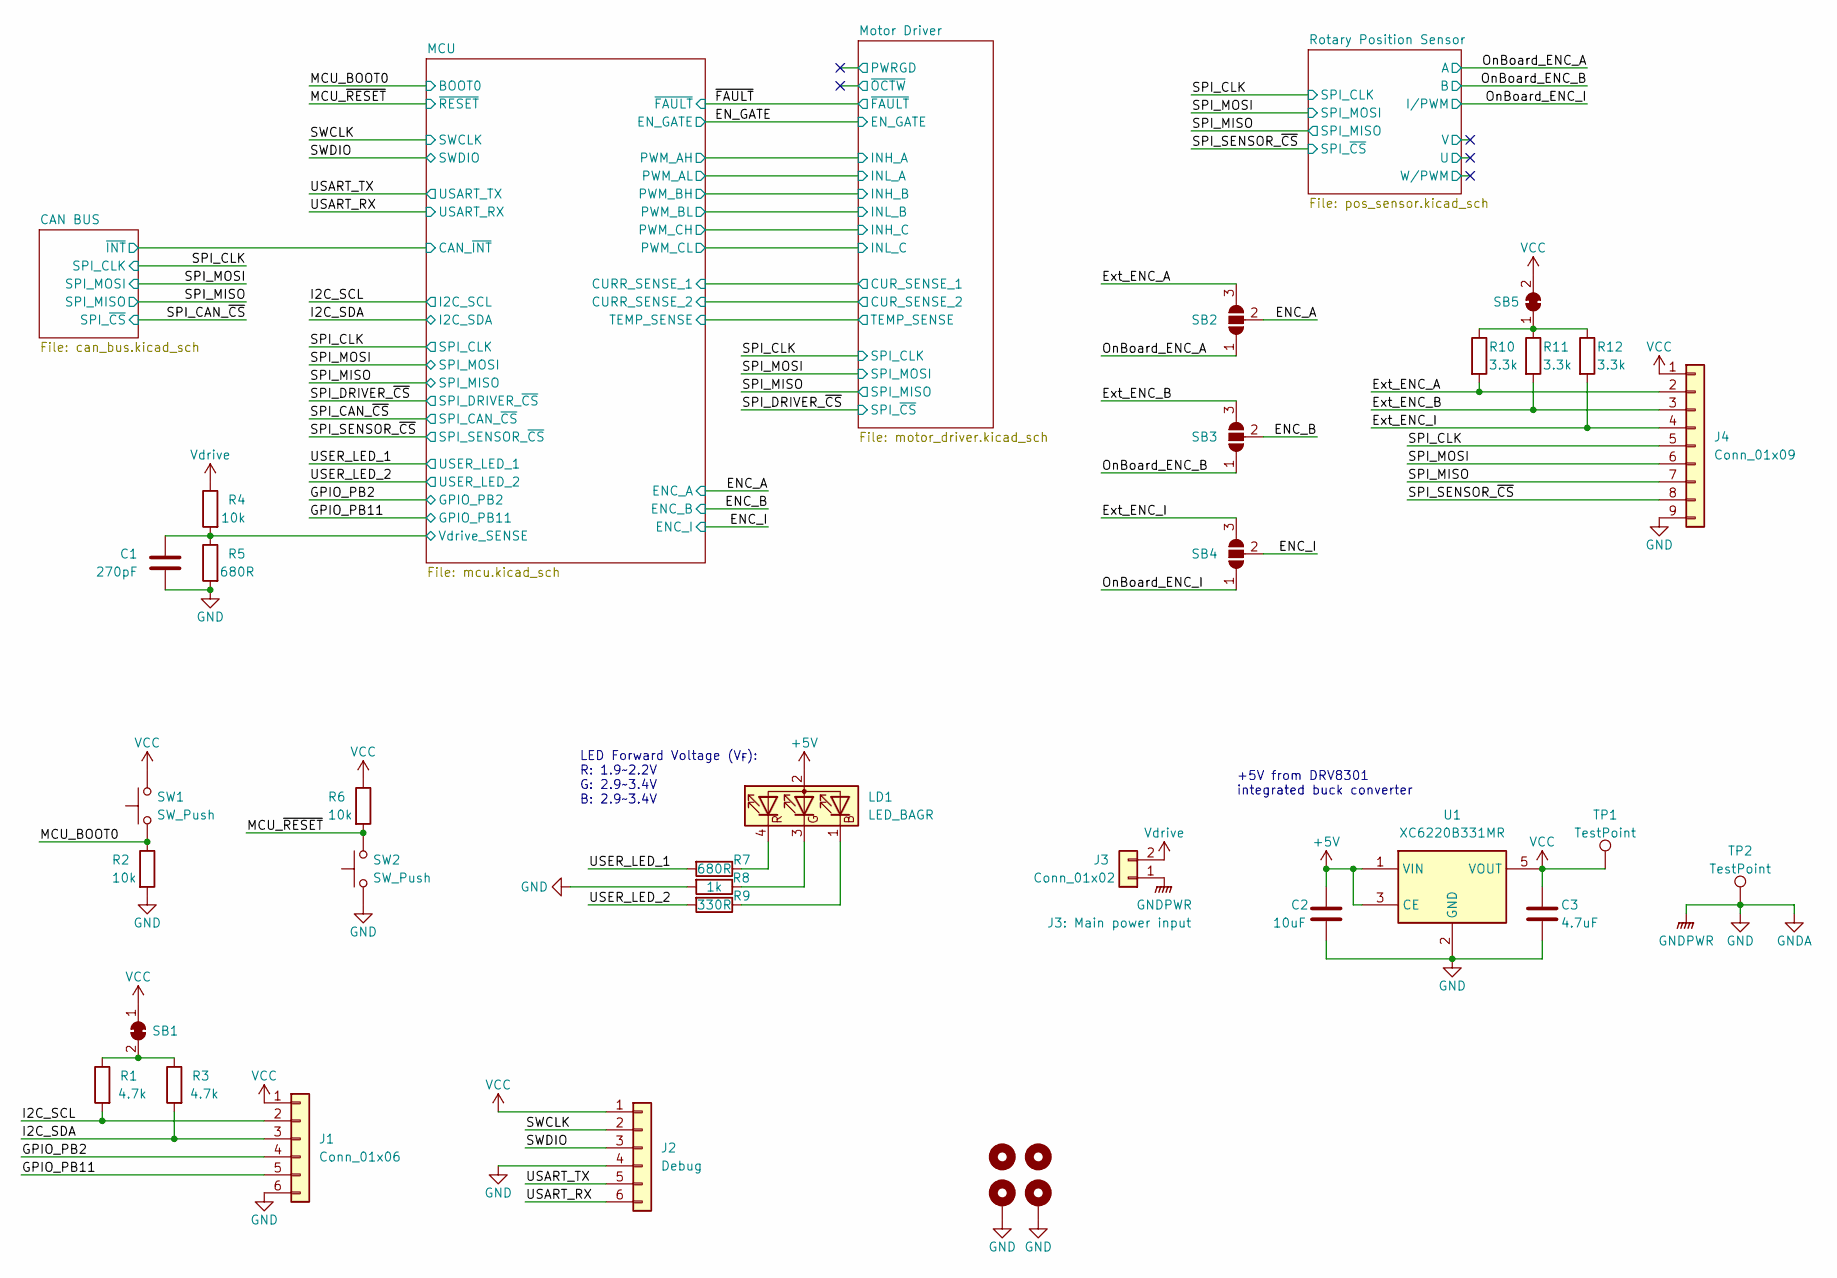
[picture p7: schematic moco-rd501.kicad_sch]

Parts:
C1: 270pF; C_0402_1005Metric; MFR.Part # GCM1555C1H271JA16D; JLCPCB Part # C524551
C2: 10uF; C_0402_1005Metric; MFR.Part # CL05A106MQ5NUNC; JLCPCB Part # C15525
C3: 4.7uF; C_0402_1005Metric; MFR.Part # CL05A475MP5NRNC; JLCPCB Part # C23733
H1, H3: MountingHole; MountingHole_2.2mm_M2_ISO14580
H2, H4: MountingHole_Pad; MountingHole_2.2mm_M2_Pad_Via
J1: Conn_01x06; JST_GH_SM06B-GHS-TB_1x06-1MP_P1.25mm_Horizontal; MFR.Part # GH1.25-6PWBPZ; JLCPCB Part # C2829255
J2: Debug; PinHeader_1x06_P2.54mm_Vertical
J3: Conn_01x02; AMASS_XT60-M_1x02_P7.20mm_Vertical; MFR.Part # XT60; JLCPCB Part # C98733
J4: Conn_01x09; JST_GH_SM09B-GHS-TB_1x09-1MP_P1.25mm_Horizontal; MFR.Part # GH1.25-9PWBPZ; JLCPCB Part # C2829258
LD1: LED_BAGR; RGB LED 1.6x1.6mm; MFR.Part # E6C0606RGBC3UDA; JLCPCB Part # C375569
R1, R3: 4.7k; R_0402_1005Metric; MFR.Part # 0402WGF4701TCE; JLCPCB Part # C25900
R2, R4, R6: 10k; R_0402_1005Metric; MFR.Part # 0402WGF1002TCE; JLCPCB Part # C25744
R5, R7: 680R; R_0402_1005Metric; MFR.Part # 0402WGF6800TCE; JLCPCB Part # C25130
R8: 1k; R_0402_1005Metric; MFR.Part # 0402WGF1001TCE; JLCPCB Part # C11702
R9: 330R; R_0402_1005Metric; MFR.Part # 0402WGF3300TCE; JLCPCB Part # C25104
R10, R11, R12: 3.3k; R_0402_1005Metric; MFR.Part # 0402WGF3301TCE; JLCPCB Part # C25890
SB1, SB5: SolderJumper_2_Bridged; SolderJumper-2_P1.3mm_Bridged_RoundedPad1.0x1.5mm
SB2, SB3, SB4: Jumper_3_Bridged12; SolderJumper-3_P1.3mm_Open_RoundedPad1.0x1.5mm_NumberLabels
SW1, SW2: SW_Push; SW_SPST_CK_RS282G05A3; MFR.Part # TS-1092S-B3D2-G; JLCPCB Part # C520860
TP1, TP2: TestPoint; TestPoint_Pad_D2.0mm
U1: XC6220B331MR; SOT-23-5; MFR.Part # XC6220B331MR-G; JLCPCB Part # C86534

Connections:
+5V: C2.1, LD1.2 (A), U1.1 (VIN), U1.3 (CE); also elsewhere on the board
/ENC_A: SB2.2 (C); also elsewhere on the board
/ENC_B: SB3.2 (C); also elsewhere on the board
/ENC_I: SB4.2 (C); also elsewhere on the board
/Ext_ENC_A: J4.2, R10.2, SB2.3 (B)
/Ext_ENC_B: J4.3, R11.2, SB3.3 (B)
/Ext_ENC_I: J4.4, R12.2, SB4.3 (B)
/GPIO_PB2: J1.4; also elsewhere on the board
/GPIO_PB11: J1.5; also elsewhere on the board
/I2C_SCL: J1.2, R1.2; also elsewhere on the board
/I2C_SDA: J1.3, R3.2; also elsewhere on the board
/MCU/Vdrive_SENSE: C1.1, R4.2, R5.1; also elsewhere on the board
/MCU_BOOT0: R2.1, SW1.1; also elsewhere on the board
/MCU_~RESET: R6.2, SW2.2; also elsewhere on the board
/OnBoard_ENC_A: SB2.1 (A); also elsewhere on the board
/OnBoard_ENC_B: SB3.1 (A); also elsewhere on the board
/OnBoard_ENC_I: SB4.1 (A); also elsewhere on the board
/SPI_CLK: J4.5; also elsewhere on the board
/SPI_MISO: J4.7; also elsewhere on the board
/SPI_MOSI: J4.6; also elsewhere on the board
/SPI_SENSOR_~CS: J4.8; also elsewhere on the board
/SWCLK: J2.2; also elsewhere on the board
/SWDIO: J2.3; also elsewhere on the board
/USART_RX: J2.6; also elsewhere on the board
/USART_TX: J2.5; also elsewhere on the board
/USER_LED_1: R7.2; also elsewhere on the board
/USER_LED_2: R9.2; also elsewhere on the board
GND: C1.2, C2.2, C3.2, H2.1, H4.1, J1.6, J2.4, J3.1, J4.9, R2.2, R5.2, R8.2, SW2.1, TP2.1, U1.2 (GND); also elsewhere on the board
unnamed: LD1.1 (BK), R9.1
unnamed: LD1.3 (GK), R8.1
unnamed: LD1.4 (RK), R7.1
unnamed: R1.1, R3.1, SB1.2 (B)
unnamed: R10.1, R11.1, R12.1, SB5.1 (A)
VCC: C3.1, J1.1, J2.1, J4.1, R6.1, SB1.1 (A), SB5.2 (B), SW1.2, TP1.1, U1.5 (VOUT); also elsewhere on the board
Vdrive: J3.2, R4.1; also elsewhere on the board

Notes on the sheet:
LED Forward Voltage (V_{F}): R: 1.9~2.2V G: 2.9~3.4V B: 2.9~3.4V
+5V from DRV8301 integrated buck converter

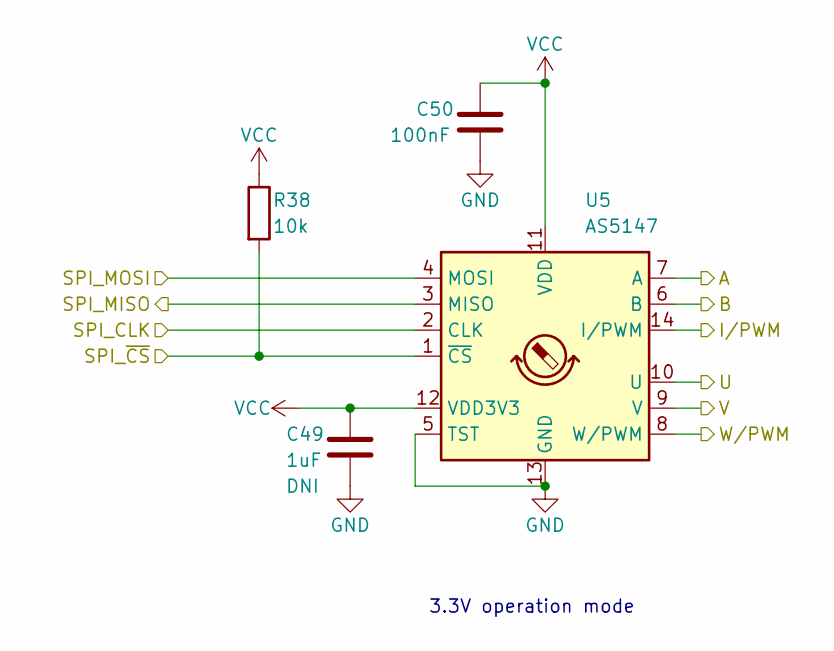
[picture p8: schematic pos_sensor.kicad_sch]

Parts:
C49: 1uF; C_0603_1608Metric
C50: 100nF; C_0603_1608Metric
R38: 10k; R_0402_1005Metric; MFR.Part # 0402WGF1002TCE; JLCPCB Part # C25744
U5: AS5147; TSSOP-14_4.4x5mm_P0.65mm; MFR.Part # AS5147P-HTSM; JLCPCB Part # C481876

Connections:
/OnBoard_ENC_A: U5.7 (A); also elsewhere on the board
/OnBoard_ENC_B: U5.6 (B); also elsewhere on the board
/OnBoard_ENC_I: U5.14 (I/PWM); also elsewhere on the board
/Rotary Position Sensor/U: U5.10 (U)
/Rotary Position Sensor/V: U5.9 (V)
/Rotary Position Sensor/W/PWM: U5.8 (W/PWM)
/SPI_CLK: U5.2 (CLK); also elsewhere on the board
/SPI_MISO: U5.3 (MISO); also elsewhere on the board
/SPI_MOSI: U5.4 (MOSI); also elsewhere on the board
/SPI_SENSOR_~CS: R38.2, U5.1 (~CS); also elsewhere on the board
GND: C49.2, C50.2, U5.5 (TST), U5.13 (GND); also elsewhere on the board
VCC: C49.1, C50.1, R38.1, U5.11 (VDD), U5.12 (VDD3V3); also elsewhere on the board

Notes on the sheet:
3.3V operation mode

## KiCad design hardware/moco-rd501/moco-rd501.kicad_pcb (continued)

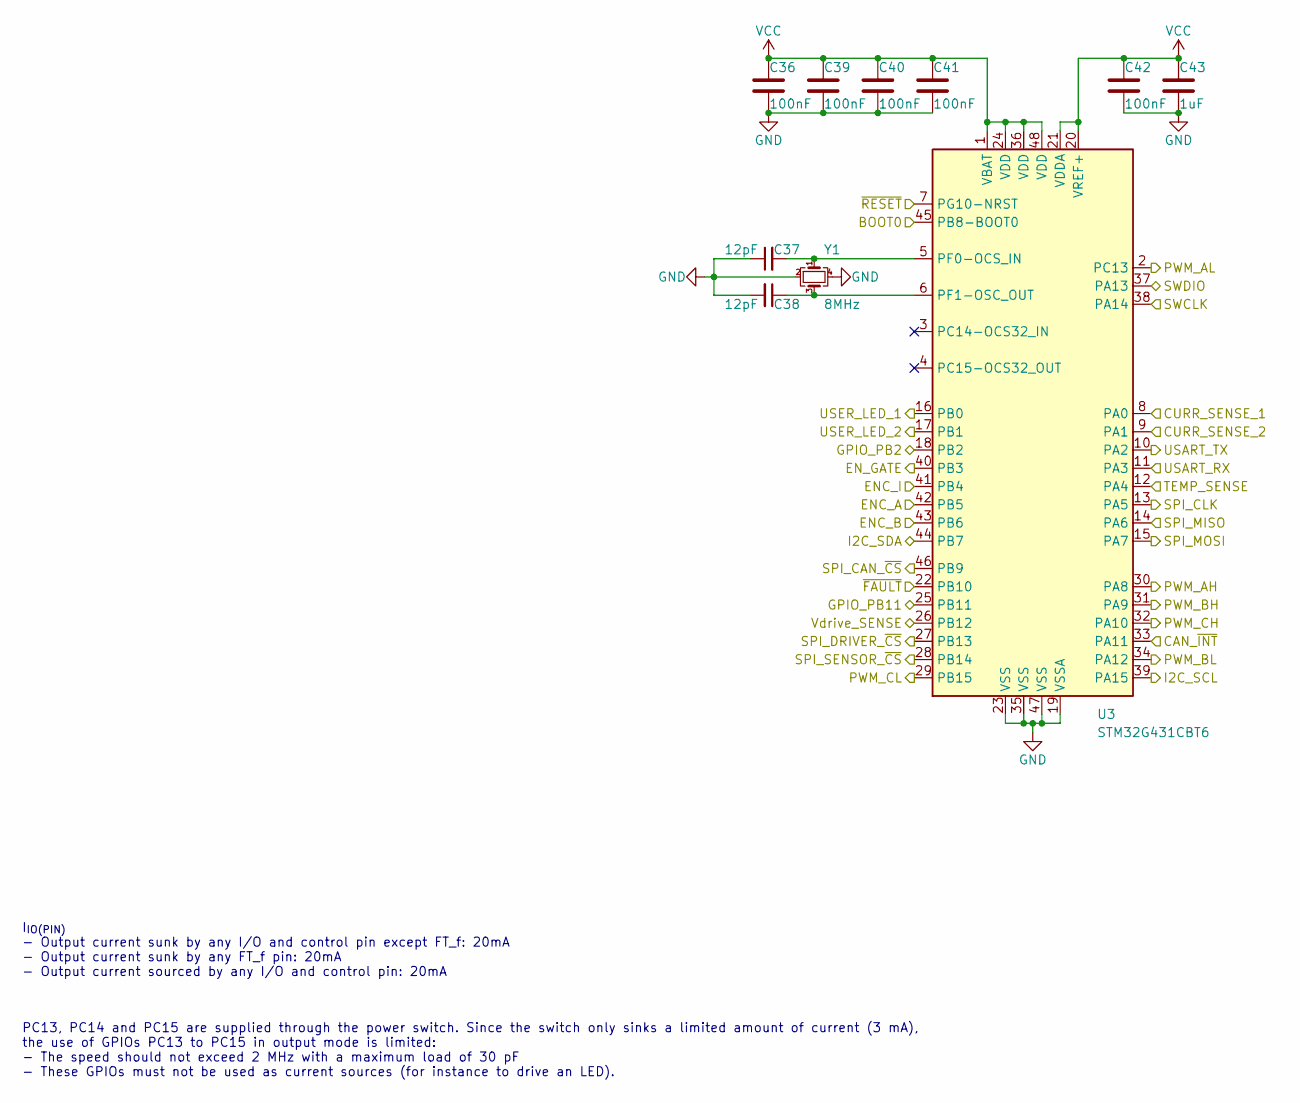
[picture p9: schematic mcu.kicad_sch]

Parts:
C36, C39, C40, C41, C42: 100nF; C_0402_1005Metric; MFR.Part # CL05B104KO5NNNC; JLCPCB Part # C1525
C37, C38: 12pF; C_0402_1005Metric; MFR.Part # 0402CG120J500NT; JLCPCB Part # C1547
C43: 1uF; C_0402_1005Metric; MFR.Part # CL05A105KA5NQNC; JLCPCB Part # C52923
U3: STM32G431CBT6; LQFP-48_7x7mm_P0.5mm; MFR.Part # STM32G431CBT6; JLCPCB Part # C529355
Y1: 8MHz; Crystal_SMD_3225-4Pin_3.2x2.5mm; MFR.Part # 1C208000BC0R; JLCPCB Part # C57131

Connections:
/CAN BUS/~INT: U3.33 (PA11); also elsewhere on the board
/ENC_A: U3.42 (PB5); also elsewhere on the board
/ENC_B: U3.43 (PB6); also elsewhere on the board
/ENC_I: U3.41 (PB4); also elsewhere on the board
/EN_GATE: U3.40 (PB3); also elsewhere on the board
/GPIO_PB2: U3.18 (PB2); also elsewhere on the board
/GPIO_PB11: U3.25 (PB11); also elsewhere on the board
/I2C_SCL: U3.39 (PA15); also elsewhere on the board
/I2C_SDA: U3.44 (PB7); also elsewhere on the board
/MCU/CURR_SENSE_1: U3.8 (PA0); also elsewhere on the board
/MCU/CURR_SENSE_2: U3.9 (PA1); also elsewhere on the board
/MCU/PWM_AH: U3.30 (PA8); also elsewhere on the board
/MCU/PWM_AL: U3.2 (PC13); also elsewhere on the board
/MCU/PWM_BH: U3.31 (PA9); also elsewhere on the board
/MCU/PWM_BL: U3.34 (PA12); also elsewhere on the board
/MCU/PWM_CH: U3.32 (PA10); also elsewhere on the board
/MCU/PWM_CL: U3.29 (PB15); also elsewhere on the board
/MCU/TEMP_SENSE: U3.12 (PA4); also elsewhere on the board
/MCU/Vdrive_SENSE: U3.26 (PB12); also elsewhere on the board
/MCU_BOOT0: U3.45 (PB8-BOOT0); also elsewhere on the board
/MCU_~RESET: U3.7 (PG10-NRST); also elsewhere on the board
/SPI_CAN_~CS: U3.46 (PB9); also elsewhere on the board
/SPI_CLK: U3.13 (PA5); also elsewhere on the board
/SPI_DRIVER_~CS: U3.27 (PB13); also elsewhere on the board
/SPI_MISO: U3.14 (PA6); also elsewhere on the board
/SPI_MOSI: U3.15 (PA7); also elsewhere on the board
/SPI_SENSOR_~CS: U3.28 (PB14); also elsewhere on the board
/SWCLK: U3.38 (PA14); also elsewhere on the board
/SWDIO: U3.37 (PA13); also elsewhere on the board
/USART_RX: U3.11 (PA3); also elsewhere on the board
/USART_TX: U3.10 (PA2); also elsewhere on the board
/USER_LED_1: U3.16 (PB0); also elsewhere on the board
/USER_LED_2: U3.17 (PB1); also elsewhere on the board
/~FAULT: U3.22 (PB10); also elsewhere on the board
GND: C36.2, C37.1, C38.2, C39.2, C40.2, C41.2, C42.2, C43.2, U3.19 (VSSA), U3.23 (VSS), U3.35 (VSS), U3.47 (VSS), Y1.2, Y1.4; also elsewhere on the board
unnamed: C37.2, U3.5 (PF0-OCS_IN), Y1.1
unnamed: C38.1, U3.6 (PF1-OSC_OUT), Y1.3
VCC: C36.1, C39.1, C40.1, C41.1, C42.1, C43.1, U3.1 (VBAT), U3.20 (VREF+), U3.21 (VDDA), U3.24 (VDD), U3.36 (VDD), U3.48 (VDD); also elsewhere on the board

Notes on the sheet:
I_{IO(PIN)} - Output current sunk by any I/O and control pin except FT_f: 20mA - Output current sunk by any FT_f pin: 20mA - Output current sourced by any I/O and control pin: 20mA
PC13, PC14 and PC15 are supplied through the power switch. Since the switch only sinks a limited amount of current (3 mA), the use of GPIOs PC13 to PC15 in output mode is limited: - The speed should not exceed 2 MHz with a maximum load of 30 pF - These GPIOs must not be used as current sources (for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

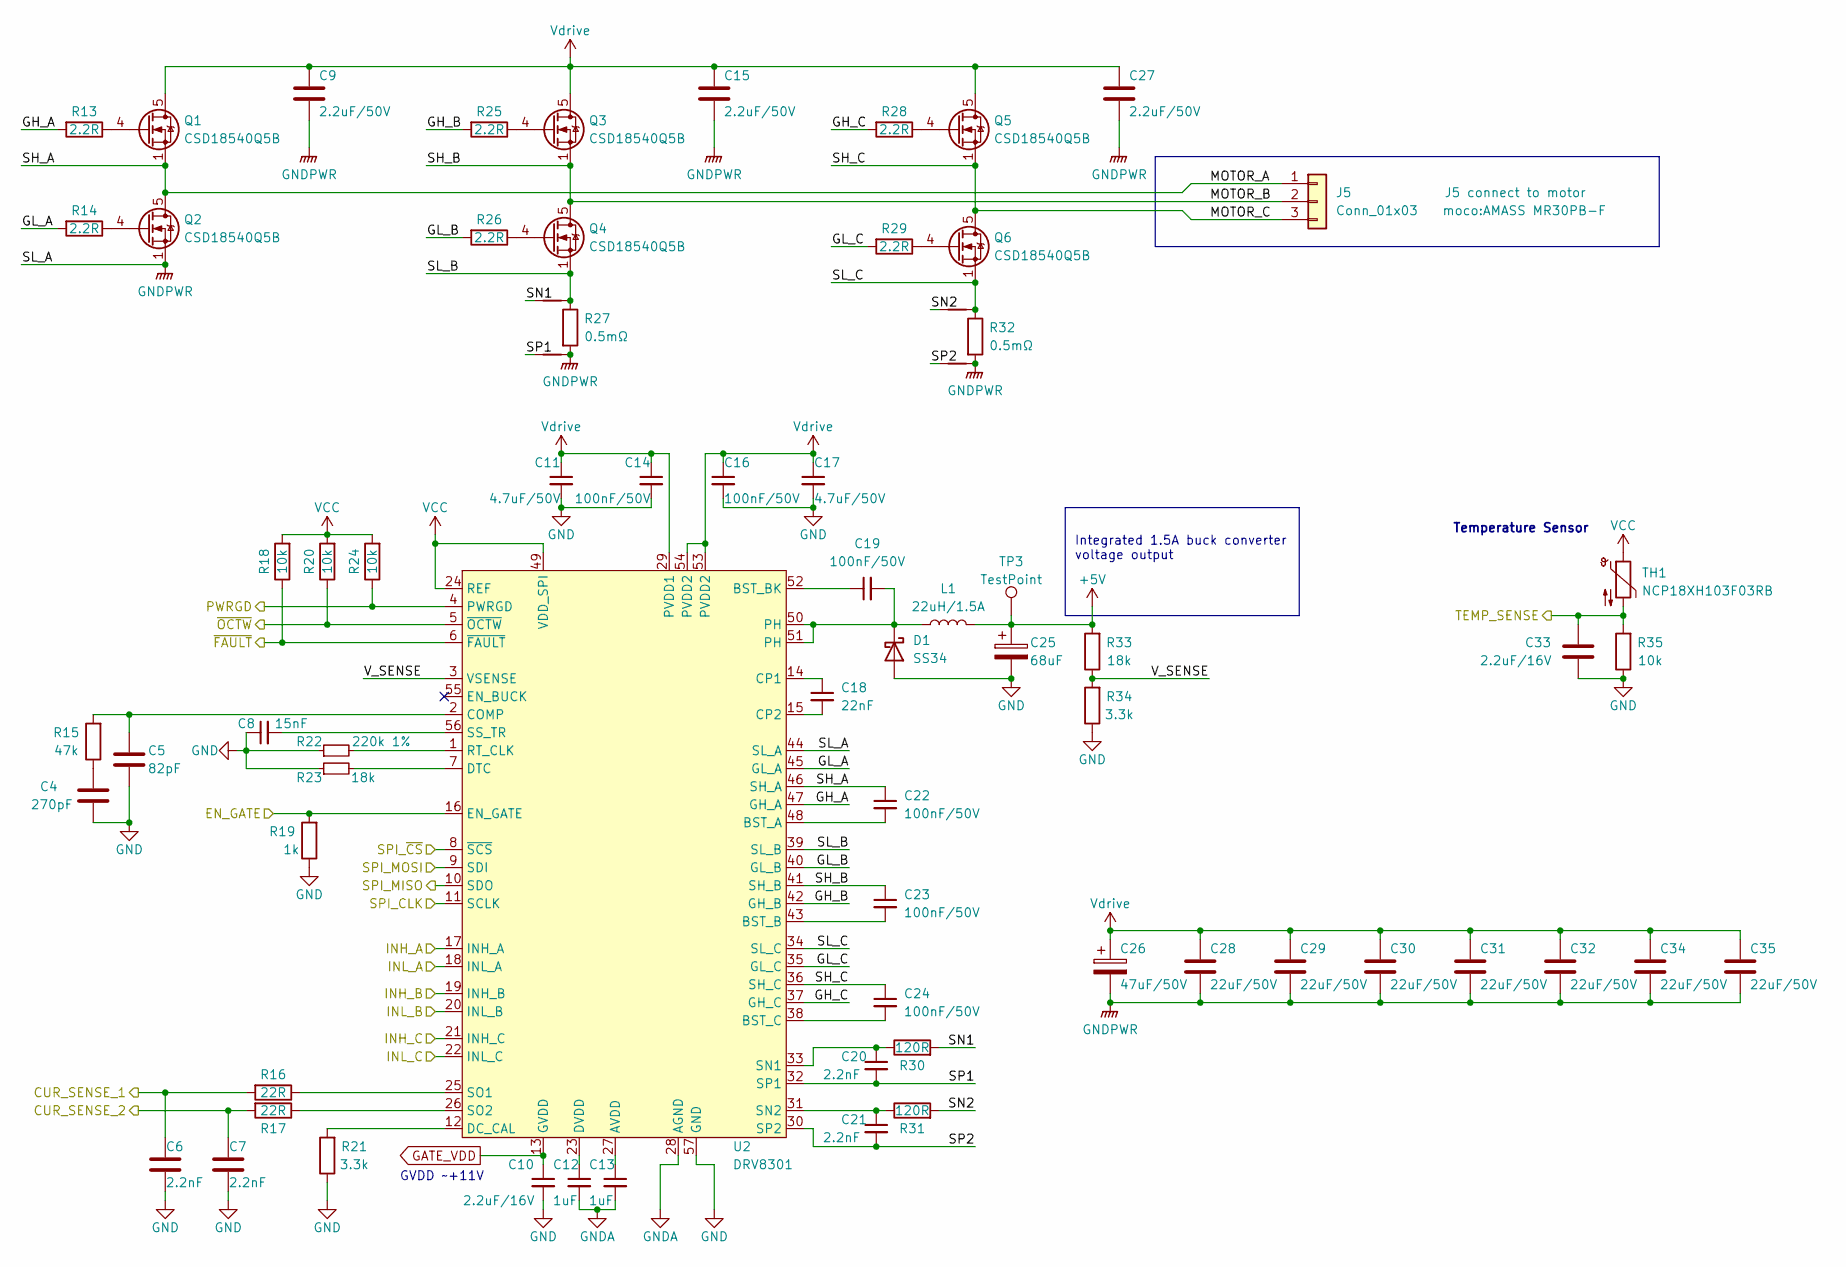
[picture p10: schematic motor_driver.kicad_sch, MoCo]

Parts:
C4: 270pF; C_0402_1005Metric; MFR.Part # GCM1555C1H271JA16D; JLCPCB Part # C524551
C5: 82pF; C_0402_1005Metric; MFR.Part # CC0402JRNPO9BN820; JLCPCB Part # C107011
C6, C7, C20, C21: 2.2nF; C_0603_1608Metric; MFR.Part # 0603B222K500NT; JLCPCB Part # C1604
C8: 15nF; C_0402_1005Metric; MFR.Part # CC0402KRX7R9BB153; JLCPCB Part # C114405
C9, C15, C27: 2.2uF/50V; C_1206_3216Metric; MFR.Part # CL31B225KBHNNNE; JLCPCB Part # C50254
C10, C33: 2.2uF/16V; C_0402_1005Metric; MFR.Part # 0402X225K160NT; JLCPCB Part # C501836
C11, C17: 4.7uF/50V; C_1206_3216Metric; MFR.Part # 1206B475K500NT; JLCPCB Part # C29823
C12, C13: 1uF; C_0402_1005Metric; MFR.Part # CL05A105KA5NQNC; JLCPCB Part # C52923
C14, C16, C19, C22, C23, C24: 100nF/50V; C_0603_1608Metric; MFR.Part # CC0603KRX7R9BB104; JLCPCB Part # C14663
C18: 22nF; C_0402_1005Metric; MFR.Part # 0402B223K500NT; JLCPCB Part # C1532
C25: 68uF; CP_EIA-6032-28_Kemet-C; MFR.Part # TAJC686K016RNJ; JLCPCB Part # C7220
C26: 47uF/50V; CP_Elec_6.3x7.7; MFR.Part # VES470M1HTR-0607; JLCPCB Part # C108053
C28, C29, C30, C31, C32, C34, C35: 22uF/50V; C_1210_3225Metric_Pad1.33x2.70mm_HandSolder
D1: SS34; D_SMA; MFR.Part # SS34; JLCPCB Part # C8678
J5: Conn_01x03; AMASS MR30PB-F; MFR.Part # MR30PB-F
L1: 22uH/1.5A; L_Bourns-SRN8040_8x8.15mm; MFR.Part # CKCS8040-22uH/M; JLCPCB Part # C354640
NT1, NT2, NT3, NT4: NetTie_2; NetTie-2_SMD_Pad0.5mm
Q1, Q2, Q3, Q4, Q5, Q6: CSD18540Q5B; TDSON-8-1; MFR.Part # CSD18540Q5B; JLCPCB Part # C86513
R13, R14, R25, R26, R28, R29: 2.2R; R_0603_1608Metric; MFR.Part # 0603WAF220KT5E; JLCPCB Part # C22939
R15: 47k; R_0402_1005Metric; MFR.Part # 0402WGF4702TCE; JLCPCB Part # C25792
R16, R17: 22R; R_0402_1005Metric; MFR.Part # 0402WGF220JTCE; JLCPCB Part # C25092
R18, R20, R24, R35: 10k; R_0402_1005Metric; MFR.Part # 0402WGF1002TCE; JLCPCB Part # C25744
R19: 1k; R_0402_1005Metric; MFR.Part # 0402WGF1001TCE; JLCPCB Part # C11702
R21, R34: 3.3k; R_0402_1005Metric; MFR.Part # 0402WGF3301TCE; JLCPCB Part # C25890
R22: 220k 1%; R_0402_1005Metric; MFR.Part # 0402WGF2203TCE; JLCPCB Part # C25767
R23, R33: 18k; R_0402_1005Metric; MFR.Part # 0402WGF1802TCE; JLCPCB Part # C25762
R27, R32: 0.5mΩ; R_2512_6332Metric; MFR.Part # ASR-M-3-0.5F; JLCPCB Part # C469426
R30, R31: 120R; R_0402_1005Metric; MFR.Part # 0402WGF1200TCE; JLCPCB Part # C25079
TH1: NCP18XH103F03RB; R_0603_1608Metric; MFR.Part # NCP18XH103F03RB; JLCPCB Part # C13564
TP3: TestPoint; TestPoint_Pad_D2.0mm
U2: DRV8301; HTSSOP-56-1EP_6.1x14mm_P0.5mm_EP3.61x6.35mm; MFR.Part # DRV8301DCAR; JLCPCB Part # C98969

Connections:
+5V: C25.1, L1.2, R33.2, TP3.1; also elsewhere on the board
/EN_GATE: R19.2, U2.16 (EN_GATE); also elsewhere on the board
/MCU/CURR_SENSE_1: C6.1, R16.2; also elsewhere on the board
/MCU/CURR_SENSE_2: C7.1, R17.2; also elsewhere on the board
/MCU/PWM_AH: U2.17 (INH_A); also elsewhere on the board
/MCU/PWM_AL: U2.18 (INL_A); also elsewhere on the board
/MCU/PWM_BH: U2.19 (INH_B); also elsewhere on the board
/MCU/PWM_BL: U2.20 (INL_B); also elsewhere on the board
/MCU/PWM_CH: U2.21 (INH_C); also elsewhere on the board
/MCU/PWM_CL: U2.22 (INL_C); also elsewhere on the board
/MCU/TEMP_SENSE: C33.1, R35.2, TH1.2; also elsewhere on the board
/Motor Driver/GH_A: R13.2, U2.47 (GH_A)
/Motor Driver/GH_B: R25.2, U2.42 (GH_B)
/Motor Driver/GH_C: R28.2, U2.37 (GH_C)
/Motor Driver/GL_A: R14.2, U2.45 (GL_A)
/Motor Driver/GL_B: R26.2, U2.40 (GL_B)
/Motor Driver/GL_C: R29.2, U2.35 (GL_C)
/Motor Driver/MOTOR_A: C22.1, J5.1, Q1.1 (S), Q1.2 (S), Q1.3 (S), Q2.5 (D), U2.46 (SH_A)
/Motor Driver/MOTOR_B: C23.1, J5.2, Q3.1 (S), Q3.2 (S), Q3.3 (S), Q4.5 (D), U2.41 (SH_B)
/Motor Driver/MOTOR_C: C24.1, J5.3, Q5.1 (S), Q5.2 (S), Q5.3 (S), Q6.5 (D), U2.36 (SH_C)
/Motor Driver/PWRGD: R24.1, U2.4 (PWRGD)
/Motor Driver/SL_B: NT1.2, Q4.1 (S), Q4.2 (S), Q4.3 (S), R27.1, U2.39 (SL_B)
/Motor Driver/SL_C: NT3.2, Q6.1 (S), Q6.2 (S), Q6.3 (S), R32.1, U2.34 (SL_C)
/Motor Driver/SN1: NT1.1, R30.2
/Motor Driver/SN2: NT3.1, R31.2
/Motor Driver/SP1: C20.2, NT2.1, U2.32 (SP1)
/Motor Driver/SP2: C21.2, NT4.1, U2.30 (SP2)
/Motor Driver/V_SENSE: R33.1, R34.2, U2.3 (VSENSE)
/Motor Driver/~OCTW: R20.1, U2.5 (~OCTW)
/SPI_CLK: U2.11 (SCLK); also elsewhere on the board
/SPI_DRIVER_~CS: U2.8 (~SCS); also elsewhere on the board
/SPI_MISO: U2.10 (SDO); also elsewhere on the board
/SPI_MOSI: U2.9 (SDI); also elsewhere on the board
/~FAULT: R18.1, U2.6 (~FAULT); also elsewhere on the board
GATE_VDD: C10.1, U2.13 (GVDD)
GND: C4.2, C5.2, C6.2, C7.2, C8.1, C9.2, C10.2, C11.2, C12.2, C13.2, C14.2, C15.2, C16.2, C17.2, C25.2, C26.2, C27.2, C28.2, C29.2, C30.2, C31.2, C32.2, C33.2, C34.2, C35.2, D1.2 (A), NT2.2, NT4.2, Q2.1 (S), Q2.2 (S), Q2.3 (S), R19.1, R21.1, R22.1, R23.1, R27.2, R32.2, R34.1, R35.1, U2.28 (AGND), U2.44 (SL_A), U2.57 (GND); also elsewhere on the board
unnamed: C4.1, R15.1
unnamed: C5.1, R15.2, U2.2 (COMP)
unnamed: C8.2, U2.56 (SS_TR)
unnamed: C12.1, U2.23 (DVDD)
unnamed: C13.1, U2.27 (AVDD)
unnamed: C18.1, U2.14 (CP1)
unnamed: C18.2, U2.15 (CP2)
unnamed: C19.1, U2.52 (BST_BK)
unnamed: C19.2, D1.1 (K), L1.1, U2.50 (PH), U2.51 (PH)
unnamed: C20.1, R30.1, U2.33 (SN1)
unnamed: C21.1, R31.1, U2.31 (SN2)
unnamed: C22.2, U2.48 (BST_A)
unnamed: C23.2, U2.43 (BST_B)
unnamed: C24.2, U2.38 (BST_C)
unnamed: Q1.4 (G), R13.1
unnamed: Q2.4 (G), R14.1
unnamed: Q3.4 (G), R25.1
unnamed: Q4.4 (G), R26.1
unnamed: Q5.4 (G), R28.1
unnamed: Q6.4 (G), R29.1
unnamed: R16.1, U2.25 (SO1)
unnamed: R17.1, U2.26 (SO2)
unnamed: R21.2, U2.12 (DC_CAL)
unnamed: R22.2, U2.1 (RT_CLK)
unnamed: R23.2, U2.7 (DTC)
VCC: R18.2, R20.2, R24.2, TH1.1, U2.24 (REF), U2.49 (VDD_SPI); also elsewhere on the board
Vdrive: C9.1, C11.1, C14.1, C15.1, C16.1, C17.1, C26.1, C27.1, C28.1, C29.1, C30.1, C31.1, C32.1, C34.1, C35.1, Q1.5 (D), Q3.5 (D), Q5.5 (D), U2.29 (PVDD1), U2.53 (PVDD2), U2.54 (PVDD2); also elsewhere on the board

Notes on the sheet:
Integrated 1.5A buck converter voltage output
Temperature Sensor
GVDD ~+11V

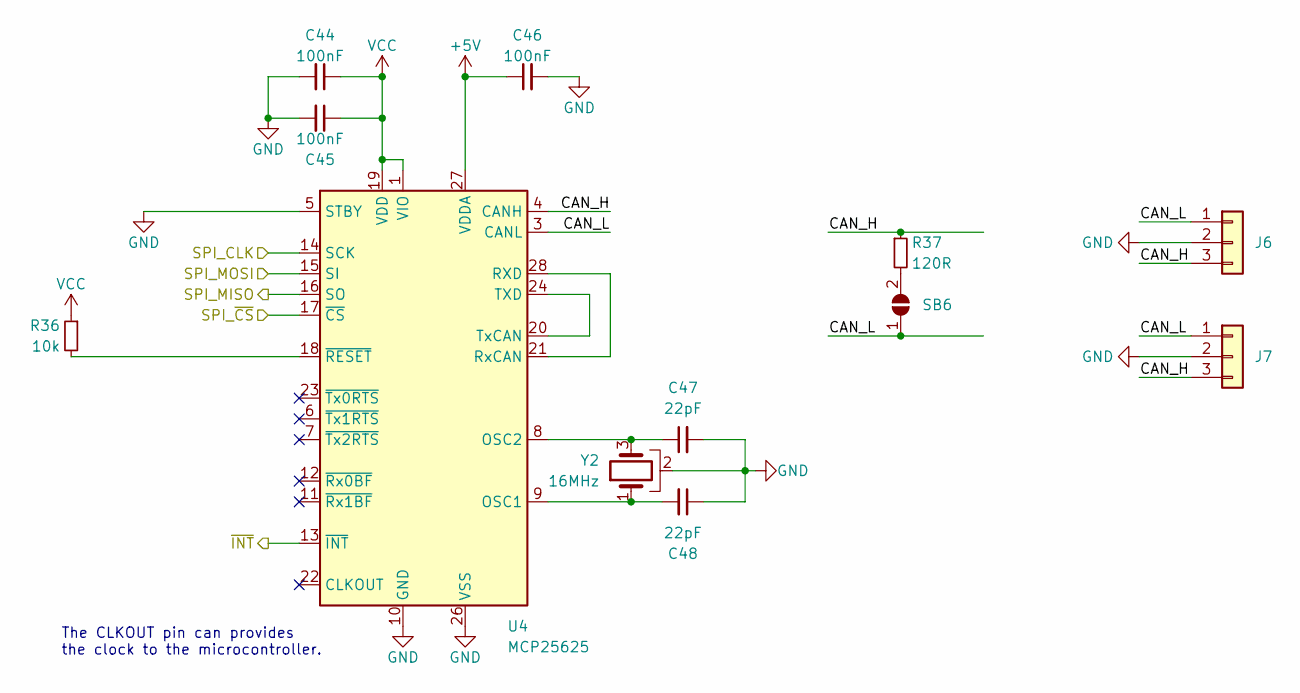
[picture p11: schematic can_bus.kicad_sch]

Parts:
C44, C45, C46: 100nF; C_0402_1005Metric; MFR.Part # CL05B104KO5NNNC; JLCPCB Part # C1525
C47, C48: 22pF; C_0402_1005Metric; MFR.Part # 0402CG220J500NT; JLCPCB Part # C1555
J6, J7: Conn_02x02_Top_Bottom; JST_GH_SM03B-GHS-TB_1x03-1MP_P1.25mm_Horizontal; MFR.Part # GH1.25-3PWBPZ; JLCPCB Part # C2829252
R36: 10k; R_0402_1005Metric; MFR.Part # 0402WGF1002TCE; JLCPCB Part # C25744
R37: 120R; R_0402_1005Metric; MFR.Part # 0402WGF1200TCE; JLCPCB Part # C25079
SB6: SolderJumper_2_Open; SolderJumper-2_P1.3mm_Open_TrianglePad1.0x1.5mm
U4: MCP25625; QFN-28-1EP_6x6mm_P0.65mm_EP4.25x4.25mm; MFR.Part # MCP25625T-E/ML; JLCPCB Part # C191253
Y2: 16MHz; Crystal_SMD_3225-4Pin_3.2x2.5mm; MFR.Part # X322516MLB4SI; JLCPCB Part # C13738

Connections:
+5V: C46.1, U4.27 (VDDA); also elsewhere on the board
/CAN BUS/CAN_H: J6.3, J7.3, R37.1, U4.4 (CANH)
/CAN BUS/CAN_L: J6.1, J7.1, SB6.1 (A), U4.3 (CANL)
/CAN BUS/~INT: U4.13 (~INT); also elsewhere on the board
/SPI_CAN_~CS: U4.17 (~CS); also elsewhere on the board
/SPI_CLK: U4.14 (SCK); also elsewhere on the board
/SPI_MISO: U4.16 (SO); also elsewhere on the board
/SPI_MOSI: U4.15 (SI); also elsewhere on the board
GND: C44.2, C45.2, C46.2, C47.2, C48.1, J6.2, J7.2, U4.5 (STBY), U4.10 (GND), U4.26 (VSS), Y2.2; also elsewhere on the board
unnamed: C47.1, U4.8 (OSC2), Y2.3
unnamed: C48.2, U4.9 (OSC1), Y2.1
unnamed: R36.2, U4.18 (~RESET)
unnamed: R37.2, SB6.2 (B)
unnamed: U4.20 (TxCAN), U4.24 (TXD)
unnamed: U4.21 (RxCAN), U4.28 (RXD)
VCC: C44.1, C45.1, R36.1, U4.1 (VIO), U4.19 (VDD); also elsewhere on the board

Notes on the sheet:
The CLKOUT pin can provides the clock to the microcontroller.

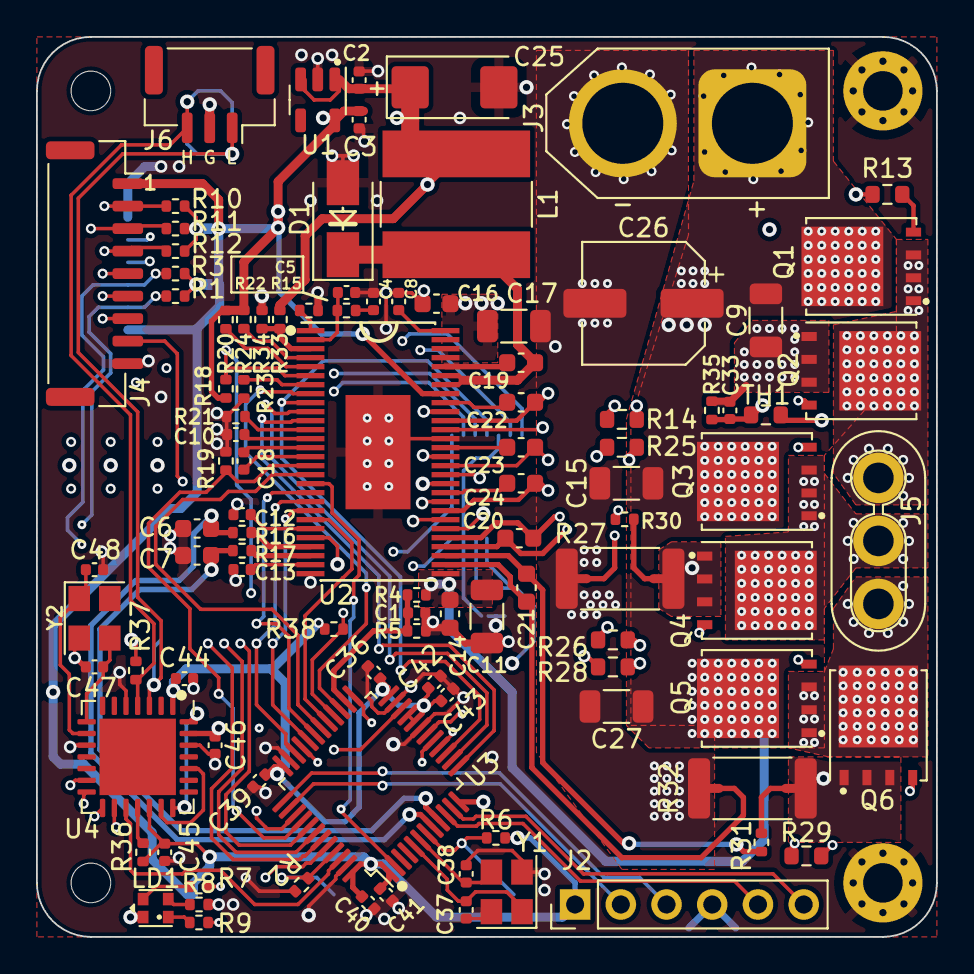
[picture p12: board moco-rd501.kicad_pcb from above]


Board: 4 copper layers, 50.0 x 50.0 mm, 135 parts (27 on the bottom side), 103 nets.

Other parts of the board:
kibuzzard-638C8B7C: G***; kibuzzard-638C8B7C
kibuzzard-638C8BCF: G***; kibuzzard-638C8BCF
kibuzzard-638C8E4D: G***; kibuzzard-638C8E4D
kibuzzard-638C8E29: G***; kibuzzard-638C8E29

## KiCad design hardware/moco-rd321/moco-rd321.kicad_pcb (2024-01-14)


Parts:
C1: 47uF; C_0805_2012Metric; MFR. Part# CL21A476MQYNNNE; LCSC C16780
C2: 220nF/50V; C_0805_2012Metric; MFR. Part# CL21B224KBFNNNE; LCSC C5378
C3, C7: 10uF/50V; C_0805_2012Metric; MFR. Part# GRM21BR61H106KE43L; LCSC C440198
C4, C5, C6, C8: 100nF; C_0402_1005Metric; MFR. Part# CL05B104KB54PNC; LCSC C307331
D1: STPS0560Z; D_SOD-123F; MFR. Part# STPS0560Z; LCSC C99285
H1, H2, H3, H4: MountingHole; MountingHole_2.2mm_M2_ISO14580
J1: Debug; PinHeader_2x04_P2.54mm_Vertical
J2: Serial; JST_SH_SM03B-SRSS-TB_1x03-1MP_P1.00mm_Horizontal; MFR. Part# SM03B-SRSS-TB(LF)(SN); LCSC C160403
J3: I^{2}C; JST_SH_SM03B-SRSS-TB_1x03-1MP_P1.00mm_Horizontal; MFR. Part# SM03B-SRSS-TB(LF)(SN); LCSC C160403
J4: V+; wire_2.2mm_rectagnel
J5: V-; wire_2.2mm
L1: 22uH; L_Taiyo-Yuden_MD-3030; MFR. Part# YNR3015-220M; LCSC C497564
LD1: Red; LED_0603_1608Metric; MFR. Part# KT-0603R; LCSC C2286
LD2: Blue; LED_0603_1608Metric; MFR. Part# 19-217/GHC-YR1S2/3T; LCSC C72043
NT1: NetTie_2; NetTie-2_SMD_Pad0.5mm
R1, R5: 10k; R_0402_1005Metric; MFR. Part# 0402WGF1002TCE; LCSC C25744
R2: 100k; R_0402_1005Metric; MFR. Part# 0402WGF1003TCE; LCSC C25741
R3, R4: 1k; R_0402_1005Metric; MFR. Part# 0402WGF1001TCE; LCSC C11702
SB1: SolderJumper_2_Open; SolderJumper-2_P1.3mm_Open_RoundedPad1.0x1.5mm
SW1: RESET; SW_SPST_EVQP7C; MFR. Part# 3*4mm
TP1: 3.3V; TestPoint_Pad_D1.0mm
TP2: 12V; TestPoint_Pad_D1.0mm
TP3: GND; TestPoint_Pad_D1.0mm
U1: STSPIN32F0A; VFQFN-48_7x7_EP2.8mm_Pitch0.5mm; MFR. Part# STSPIN32F0A; LCSC C1520987

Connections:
+3.3V: C1.1, C4.1, C5.1, J1.1, L1.1, R1.2, TP1.1, U1.10 (VDDA), U1.48 (VDD); also elsewhere on the board
+12V: C6.1, C7.1, R4.1, SB1.1 (A), TP2.1, U1.6 (VREG12)
/CUR_SEN_U: U1.11 (PA0); also elsewhere on the board
/CUR_SEN_V: U1.12 (PA1); also elsewhere on the board
/CUR_SEN_W: U1.19 (PB1); also elsewhere on the board
/I2C1_SCL: J3.1, U1.40 (PB6)
/I2C1_SDA: J3.2, U1.41 (PB7)
/OC_COMP: U1.24 (OC_COMP); also elsewhere on the board
/PF1: U1.5 (PF1)
/SPI_MISO: U1.17 (PA6); also elsewhere on the board
/SPI_MOSI: U1.18 (PA7); also elsewhere on the board
/SPI_SCLK: U1.16 (PA5); also elsewhere on the board
/SPI_~CS_RS: U1.39 (PA15); also elsewhere on the board
/SWCLK: J1.6, U1.38 (PA14_SWD_CLK)
/SWDIO: J1.4, U1.37 (PA13_SWD_IO)
/USART1_RX: J1.5, J2.2, U1.14 (PA3)
/USART1_TX: J1.3, J2.1, U1.13 (PA2)
/USER_LED: R3.1, U1.4 (PF0)
/VM_SENSE: R2.1, R5.2, U1.15 (PA4)
/~RESET: C8.1, J1.7, R1.1, SW1.1, U1.7 (NRST)
GND: C1.2, C2.2, C3.2, C4.2, C5.2, C6.2, C7.2, C8.2, D1.2 (A), J1.2, J1.8, J2.3, J3.3, LD1.1 (K), LD2.1 (K), NT1.2, R5.1, SW1.2, TP3.1, U1.20 (TESTMODE), U1.42 (BOOT0), U1.44 (GND), U1.49 (EPAD); also elsewhere on the board
GNDPWR: J5.1, NT1.1; also elsewhere on the board
unnamed: D1.1 (K), L1.2, U1.9 (SW)
unnamed: LD1.2 (A), R3.2
unnamed: LD2.2 (A), R4.2
VBUS: C2.1, C3.1, J4.1, R2.2, SB1.2 (B), U1.8 (VM); also elsewhere on the board

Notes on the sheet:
+15~35V Limited by the VM sensing divider resistance and capacitors max voltage
VM Sensing
VM:6.7~45V
LED
Main Power Input
MCU and Date Driver


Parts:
C9, C10, C13: 220nF/50V; C_0805_2012Metric; MFR. Part# CL21B224KBFNNNE; LCSC C5378
C11, C12, C14: 100nF/50V; C_0402_1005Metric; MFR. Part# CL05B104KB54PNC; LCSC C307331
C15: 1nF; C_0402_1005Metric; MFR. Part# 0402B102K500NT; LCSC C1523
C16, C17, C18, C19, C20, C21, C22, C23, C24, C26, C27, C28: 10uF/50V; C_0805_2012Metric; MFR. Part# GRM21BR61H106KE43L; LCSC C440198
C25: 22uF/50V; CP_Elec_5x5.8; MFR. Part# EEEFT1H220AR; LCSC C336246
J6: U; wire_2.2mm
J7: V; wire_2.2mm
J8: W; wire_2.2mm
NT2, NT3, NT4, NT5, NT6, NT7: NetTie_2; NetTie-2_SMD_Pad0.5mm
Q1, Q2, Q3: SiZ250DT; PowerPAIR_3x3S_TP; MFR. Part# SIZ250DT-T1-GE3; LCSC C3279427
R6, R7, R8, R9, R22, R25: 10R; R_0402_1005Metric; MFR. Part# 0402WGF100JTCE; LCSC C25077
R10, R11, R15, R17, R27, R31: 24k; R_0402_1005Metric; MFR. Part# 0402WGF2402TCE; LCSC C25769
R12, R13, R18, R19, R28, R32: 1.78k; R_0402_1005Metric; MFR. Part# ARG02FTC1781; LCSC C284379
R14, R16, R30: 20mΩ/3W; R_2512_6332Metric; MFR. Part# CRA2512-FZ-R020ELF; LCSC C840620
R20, R21, R33: 12k; R_0402_1005Metric; MFR. Part# 0402WGF1202TCE; LCSC C25752
R23, R26, R29: 2.2k; R_0402_1005Metric; MFR. Part# 0402WGF2201TCE; LCSC C25879
R24: 6.8k; R_0402_1005Metric; MFR. Part# 0402WGF6801TCE; LCSC C25917
U1: STSPIN32F0A; VFQFN-48_7x7_EP2.8mm_Pitch0.5mm; MFR. Part# STSPIN32F0A; LCSC C1520987

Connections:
+3.3V: R10.1, R11.1, R24.1, R27.1; also elsewhere on the board
/CUR_SEN_U: R20.2, U1.47 (OP3O); also elsewhere on the board
/CUR_SEN_V: R21.2, U1.3 (OP2O); also elsewhere on the board
/CUR_SEN_W: R33.2, U1.21 (OP1O); also elsewhere on the board
/OC_COMP: C15.1, R23.2, R24.2, R26.2, R29.2; also elsewhere on the board
/Triple Half-bridge/OUTU: C11.1, J6.1, Q1.9 (S1D2), U1.34 (OUTU)
/Triple Half-bridge/OUTV: C12.1, J7.1, Q2.9 (S1D2), U1.30 (OUTV)
/Triple Half-bridge/OUTW: C14.1, J8.1, Q3.9 (S1D2), U1.26 (OUTW)
/Triple Half-bridge/RSU+: NT2.1, R12.1, R23.1
/Triple Half-bridge/RSU-: NT4.1, R18.1
/Triple Half-bridge/RSV+: NT3.1, R13.1, R26.1
/Triple Half-bridge/RSV-: NT5.1, R19.1
/Triple Half-bridge/RSW+: NT6.1, R28.1, R29.1
/Triple Half-bridge/RSW-: NT7.1, R32.1
/Triple Half-bridge/US: NT2.2, Q1.5 (S2), Q1.6 (S2), Q1.7 (S2), R14.1
/Triple Half-bridge/VS: NT3.2, Q2.5 (S2), Q2.6 (S2), Q2.7 (S2), R16.1
/Triple Half-bridge/WS: NT6.2, Q3.5 (S2), Q3.6 (S2), Q3.7 (S2), R30.1
GND: C15.2, R15.2, R17.2, R31.2; also elsewhere on the board
GNDPWR: C9.1, C10.1, C13.1, C16.2, C17.2, C18.2, C19.2, C20.2, C21.2, C22.2, C23.2, C24.2, C25.2, C26.2, C27.2, C28.2, NT4.2, NT5.2, NT7.2, R14.2, R16.2, R30.2; also elsewhere on the board
unnamed: Q1.1 (G1), R6.2
unnamed: Q1.8 (G2), R8.2
unnamed: Q2.1 (G1), R7.2
unnamed: Q2.8 (G2), R9.2
unnamed: Q3.1 (G1), R22.2
unnamed: Q3.8 (G2), R25.2
unnamed: R22.1, U1.25 (HSW)
unnamed: R25.1, U1.28 (LSW)
unnamed: C14.2, U1.27 (VBOOTW)
unnamed: R7.1, U1.29 (HSV)
unnamed: R9.1, U1.32 (LSV)
unnamed: C12.2, U1.31 (VBOOTV)
unnamed: R6.1, U1.33 (HSU)
unnamed: R8.1, U1.36 (LSU)
unnamed: C11.2, U1.35 (VBOOTU)
unnamed: R18.2, R20.1, U1.46 (OP3N)
unnamed: R10.2, R12.2, R15.1, U1.45 (OP3P)
unnamed: R19.2, R21.1, U1.2 (OP2N)
unnamed: R11.2, R13.2, R17.1, U1.1 (OP2P)
unnamed: R32.2, R33.1, U1.22 (OP1N)
unnamed: R27.2, R28.2, R31.1, U1.23 (OP1P)
VBUS: C9.2, C10.2, C13.2, C16.1, C17.1, C18.1, C19.1, C20.1, C21.1, C22.1, C23.1, C24.1, C25.1, C26.1, C27.1, C28.1, Q1.2 (D1), Q1.3 (D1), Q1.4 (D1), Q1.10 (D1), Q2.2 (D1), Q2.3 (D1), Q2.4 (D1), Q2.10 (D1), Q3.2 (D1), Q3.3 (D1), Q3.4 (D1), Q3.10 (D1); also elsewhere on the board

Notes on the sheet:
OC_COMP_{th}
Bootstrap capacitors close to gate driver Gate resistors close to FETs
Bulk Capacitor
PA12, PB12
Gain_{max} = V_{DD}/(2*I_{max}*R_{S}) I_{max} = 12A, Gain_{max} = 6.875 Gain = R_{B}/R_{A} ≈ 6.74 Refer to ST AN5397
Overcurrent Detection
I_{max,th} = 30A, OC_COMP_{th} = 500mV, N_{S} = 3 R_{Bias} = R_{LP}*(V_{DD}-OC_COMP_{th})/(N_{S}*OC_COMP_{th}-I_{max,th}*R_{S}) ≈ 6.84kΩ Refer to ST AN4999 Table 5


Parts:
C29: 1uF; C_0402_1005Metric; MFR. Part# CL05A105KA5NQNC; LCSC C52923
U2: MA702; QFN-16-1EP_3x3mm_P0.5mm_EP1.75x1.75mm; MFR. Part# MA702GQ-Z

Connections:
+3.3V: C29.2, U2.13 (VDD); also elsewhere on the board
/ Rotary Sensor/A: U2.2 (A)
/ Rotary Sensor/B: U2.6 (B)
/ Rotary Sensor/Z: U2.3 (Z)
/SPI_MISO: U2.7 (MISO); also elsewhere on the board
/SPI_MOSI: U2.4 (MOSI); also elsewhere on the board
/SPI_SCLK: U2.12 (SCLK); also elsewhere on the board
/SPI_~CS_RS: U2.5 (~CS); also elsewhere on the board
GND: C29.1, U2.8 (GND), U2.10 (TEST), U2.17 (PAD); also elsewhere on the board

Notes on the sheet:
Internal pull-down: MOSI, MISO, SCLK, SSCK Internal pull-up: ~{CS}
SPI: - Mode: * 0 (CPOL=0, CPHA=0) or 1 (CPOL=1, CPHA=1) * Data sampled on first edge - 16-bit data frame - MSB first - ~{CS} pin active low - 25MHz clock

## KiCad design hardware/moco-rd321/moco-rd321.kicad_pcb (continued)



Board: 4 copper layers, 32.0 x 32.0 mm, 95 parts (26 on the bottom side), 58 nets.

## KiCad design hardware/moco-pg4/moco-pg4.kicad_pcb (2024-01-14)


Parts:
C1, C2: 6.8pF; C_0402_1005Metric; MFR. Part# 0402CG6R8C500NT; LCSC C1576
C3, C4, C5, C8, C9, C11: 100nF; C_0402_1005Metric; MFR. Part# CL05B104KB54PNC; LCSC C307331
C6: 10uF; C_0402_1005Metric; MFR. Part# CL05A106MQ5NUNC; LCSC C15525
C7: 220nF/50V; C_0805_2012Metric; MFR. Part# CL21B224KBFNNNE; LCSC C5378
C10, C12: 1uF; C_0402_1005Metric; MFR. Part# CL05A105KA5NQNC; LCSC C52923
C13: 10uF; C_0805_2012Metric; MFR. Part# CL21A476MQYNNNE; LCSC C16780
C35: 10uF/50V; C_0805_2012Metric; MFR. Part# GRM21BR61H106KE43L; LCSC C440198
D1: STPS0560Z; D_SOD-123F; MFR. Part# STPS0560Z; LCSC C99285
H1, H2, H3, H4: MountingHole; MountingHole_2.2mm_M2_ISO14580
J1: Debug; PinHeader_2x04_P2.54mm_Vertical
J2, J8: CAN; JST_SH_SM03B-SRSS-TB_1x03-1MP_P1.00mm_Horizontal; MFR. Part# SM03B-SRSS-TB(LF)(SN); LCSC C160403
J3: V+; wire_2.2mm_rectagnel
J4: V-; wire_2.2mm
L1: 18uH; L_Taiyo-Yuden_MD-3030; MFR. Part# YNR3015-220M; LCSC C497564
LD1: Red; LED_0603_1608Metric; MFR. Part# KT-0603R; LCSC C2286
LD2: Blue; LED_0603_1608Metric; MFR. Part# 19-217/GHC-YR1S2/3T; LCSC C72043
R1: 120R; R_0402_1005Metric_Pad0.72x0.64mm_HandSolder; MFR. Part# 0402WGF1200TCE; LCSC C25079
R2, R5, R6: 10k; R_0402_1005Metric; MFR. Part# 0402WGF1002TCE; LCSC C25744
R3: 100k; R_0402_1005Metric; MFR. Part# 0402WGF1003TCE; LCSC C25741
R4: 22k; R_0402_1005Metric; MFR. Part# 0402WGF2202TCE; LCSC C25768
R7, R8: 1k; R_0402_1005Metric; MFR. Part# 0402WGF1001TCE; LCSC C11702
SW1: RESET; SW_SPST_EVQP7C; MFR. Part# 3*4mm
TP1: GND; TestPoint_Pad_D1.0mm
U1: STSPIN32G4; VFQFPN 9X9X1.0 64 PITCH 0.5; MFR. Part# STSPIN32G4; LCSC C2858620
U2: TCAN337; SOT-23-8
Y1: 24MHz; Crystal_SMD_3225-4Pin_3.2x2.5mm; MFR. Part# X322524MSB4SI; LCSC C15643

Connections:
+3.3V: C3.2, C5.2, C6.2, C8.2, C9.2, C10.2, C11.2, C12.2, J1.1, R2.2, R4.1, U1.1 (REG3V3/VDD), U1.2 (VBAT), U1.26 (VREF+), U1.27 (VDDA), U2.3 (VCC); also elsewhere on the board
/CANH: J2.3, J8.3, R1.1, U2.7 (CANH)
/CANL: J2.1, J8.1, R1.2, U2.6 (CANL)
/CAN_FAULT: U2.5 (FAULT)
/CAN_RX: U1.47 (PA11), U2.4 (RXD)
/CAN_TX: U1.48 (PA12), U2.1 (TXD)
/OPAMP1_VINM: U1.16 (PA3); also elsewhere on the board
/OPAMP1_VINP: U1.14 (PA1); also elsewhere on the board
/OPAMP1_VOUT: U1.15 (PA2); also elsewhere on the board
/OPAMP2_VINM: U1.22 (PC5); also elsewhere on the board
/OPAMP2_VINP: U1.20 (PA7); also elsewhere on the board
/OPAMP2_VOUT: U1.19 (PA6); also elsewhere on the board
/OPAMP3_VINM: U1.25 (PB2); also elsewhere on the board
/OPAMP3_VINP: U1.23 (PB0); also elsewhere on the board
/OPAMP3_VOUT: U1.24 (PB1); also elsewhere on the board
/OSC_IN: C1.2, U1.6 (PF0), Y1.3
/OSC_OUT: C2.2, U1.7 (PF1), Y1.1
/SCREF: R4.2, R6.1, U1.52 (SCREF)
/SPI_MISO: U1.55 (PB4); also elsewhere on the board
/SPI_MOSI: U1.56 (PB5); also elsewhere on the board
/SPI_SCLK: U1.54 (PB3); also elsewhere on the board
/SPI_~CS_RS: U1.57 (PB6); also elsewhere on the board
/SWCLK: J1.5, U1.50 (PA14)
/SWDIO: J1.3, U1.49 (PA13)
/SWO: J1.7, U1.51 (PA15)
/USART_RX: J1.4, U1.59 (PB8)
/USART_TX: J1.6, U1.60 (PB9)
/USER_LED: R7.1, U1.46 (PA10)
/V_{BUS}_SENSE: R3.1, R5.2, U1.17 (PA4)
/~RESET: C4.1, R2.1, SW1.1, U1.8 (PG10)
GND: C1.1, C2.1, C3.1, C4.2, C5.1, C6.1, C7.2, C8.1, C9.1, C10.1, C11.1, C12.1, C13.2, D1.2 (A), J1.2, J1.8, J2.2, J4.1, J8.2, LD1.1 (K), LD2.1 (K), R5.1, R6.2, SW1.2, TP1.1, U1.32 (PGND), U1.65 (VSS), U2.2 (GND), Y1.2, Y1.4; also elsewhere on the board
unnamed: D1.1 (K), L1.1, U1.62 (SW)
unnamed: LD1.2 (A), R7.2
unnamed: LD2.2 (A), R8.2
VBUS: C7.1, J3.1, R3.2, U1.61 (VM); also elsewhere on the board
VCC: C13.1, L1.2, R8.1, U1.63 (VCC), U1.64 (REGIN)

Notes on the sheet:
Buck output
LDO output
LED
Main Power Input
V_{BUS} Sensing
LDO input


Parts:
C14, C17, C20: 220nF/50V; C_0805_2012Metric; MFR. Part# CL21B224KBFNNNE; LCSC C5378
C15, C18, C21: 100nF/50V; C_0402_1005Metric; MFR. Part# CL05B104KB54PNC; LCSC C307331
C16, C19, C22: 100nF; C_0402_1005Metric; MFR. Part# CL21B224KBFNNNE; LCSC C5378
C23, C24, C25, C26, C27, C28, C29, C30, C31, C33, C34: 10uF/50V; C_0805_2012Metric; MFR. Part# GRM21BR61H106KE43L; LCSC C440198
J5: A; wire_2.2mm_rectagnel
J6: B; wire_2.2mm_rectagnel
J7: C; wire_2.2mm_rectagnel
NT1, NT2, NT3, NT4, NT5, NT6: NetTie_2; NetTie-2_SMD_Pad0.5mm
Q1, Q2, Q3, Q4, Q5, Q6: DMTH4007SPS; PowerDI5060-8
R9, R10, R17, R18, R25, R26: 10R; R_0402_1005Metric; MFR. Part# 0402WGF100JTCE; LCSC C25077
R11, R14, R19, R22, R27, R30: 24k; R_0402_1005Metric; MFR. Part# 0402WGF2402TCE; LCSC C25769
R12, R15, R20, R23, R28, R31: 1.78k; R_0402_1005Metric; MFR. Part# ARG02FTC1781; LCSC C284379
R13, R21, R29: 20mΩ/3W; R_2512_6332Metric; MFR. Part# CRA2512-FZ-R020ELF; LCSC C840620
R16, R24, R32: 12k; R_0402_1005Metric; MFR. Part# 0402WGF1202TCE; LCSC C25752
U1: STSPIN32G4; VFQFPN 9X9X1.0 64 PITCH 0.5; MFR. Part# STSPIN32G4; LCSC C2858620

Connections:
+3.3V: R11.1, R19.1, R27.1; also elsewhere on the board
/OPAMP1_VINM: C16.2, R15.2, R16.1; also elsewhere on the board
/OPAMP1_VINP: R11.2, R12.2, R14.1; also elsewhere on the board
/OPAMP1_VOUT: C16.1, R16.2; also elsewhere on the board
/OPAMP2_VINM: C19.2, R23.2, R24.1; also elsewhere on the board
/OPAMP2_VINP: R19.2, R20.2, R22.1; also elsewhere on the board
/OPAMP2_VOUT: C19.1, R24.2; also elsewhere on the board
/OPAMP3_VINM: C22.2, R31.2, R32.1; also elsewhere on the board
/OPAMP3_VINP: R27.2, R28.2, R30.1; also elsewhere on the board
/OPAMP3_VOUT: C22.1, R32.2; also elsewhere on the board
/Power Stage/OUTA: C15.1, J5.1, Q1.1 (S), Q1.2 (S), Q1.3 (S), Q2.5 (D), Q2.6 (D), Q2.7 (D), Q2.8 (D), U1.42 (OUT1)
/Power Stage/OUTB: C18.1, J6.1, Q3.1 (S), Q3.2 (S), Q3.3 (S), Q4.5 (D), Q4.6 (D), Q4.7 (D), Q4.8 (D), U1.39 (OUT2)
/Power Stage/OUTC: C21.1, J7.1, Q5.1 (S), Q5.2 (S), Q5.3 (S), Q6.5 (D), Q6.6 (D), Q6.7 (D), Q6.8 (D), U1.36 (OUT3)
/Power Stage/RSA+: NT1.1, R12.1
/Power Stage/RSA-: NT2.1, R15.1
/Power Stage/RSB+: NT3.1, R20.1
/Power Stage/RSB-: NT4.1, R23.1
/Power Stage/RSC+: NT5.1, R28.1
/Power Stage/RSC-: NT6.1, R31.1
/Power Stage/S2A: NT1.2, Q2.1 (S), Q2.2 (S), Q2.3 (S), R13.1
/Power Stage/S2B: NT3.2, Q4.1 (S), Q4.2 (S), Q4.3 (S), R21.1
/Power Stage/S2C: NT5.2, Q6.1 (S), Q6.2 (S), Q6.3 (S), R29.1
GND: C14.1, C17.1, C20.1, C23.2, C24.2, C25.2, C26.2, C27.2, C28.2, C29.2, C30.2, C31.2, C33.2, C34.2, NT2.2, NT4.2, NT6.2, R13.2, R14.2, R21.2, R22.2, R29.2, R30.2; also elsewhere on the board
unnamed: Q1.4 (G), R9.2
unnamed: Q2.4 (G), R10.2
unnamed: Q3.4 (G), R17.2
unnamed: Q4.4 (G), R18.2
unnamed: Q5.4 (G), R25.2
unnamed: Q6.4 (G), R26.2
unnamed: C15.2, U1.41 (BOOT1)
unnamed: R9.1, U1.43 (GHS1)
unnamed: R10.1, U1.29 (GLS1)
unnamed: C18.2, U1.38 (BOOT2)
unnamed: R17.1, U1.40 (GHS2)
unnamed: R18.1, U1.30 (GLS2)
unnamed: C21.2, U1.35 (BOOT3)
unnamed: R25.1, U1.37 (GHS3)
unnamed: R26.1, U1.31 (GLS3)
VBUS: C14.2, C17.2, C20.2, C23.1, C24.1, C25.1, C26.1, C27.1, C28.1, C29.1, C30.1, C31.1, C33.1, C34.1, Q1.5 (D), Q1.6 (D), Q1.7 (D), Q1.8 (D), Q3.5 (D), Q3.6 (D), Q3.7 (D), Q3.8 (D), Q5.5 (D), Q5.6 (D), Q5.7 (D), Q5.8 (D); also elsewhere on the board

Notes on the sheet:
Bulk Capacitor
STM32G432 internal OP-Amp
Bootstrap capacitors close to gate driver Gate resistors close to FETs


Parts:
C36: 1uF; C_0402_1005Metric_Pad0.74x0.62mm_HandSolder; MFR. Part# CL05A105KA5NQNC; LCSC C52923
U3: MA702; QFN-16-1EP_3x3mm_P0.5mm_EP1.75x1.75mm; MFR. Part# MA702GQ-Z

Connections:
+3.3V: C36.2, U3.13 (VDD); also elsewhere on the board
/Rotary Sensor/A: U3.2 (A)
/Rotary Sensor/B: U3.6 (B)
/Rotary Sensor/Z: U3.3 (Z)
/SPI_MISO: U3.7 (MISO); also elsewhere on the board
/SPI_MOSI: U3.4 (MOSI); also elsewhere on the board
/SPI_SCLK: U3.12 (SCLK); also elsewhere on the board
/SPI_~CS_RS: U3.5 (~CS); also elsewhere on the board
GND: C36.1, U3.8 (GND), U3.10 (TEST), U3.17 (PAD); also elsewhere on the board

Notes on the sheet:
Internal pull-down: MOSI, MISO, SCLK, SSCK Internal pull-up: ~{CS}
SPI: - Mode: * 0 (CPOL=0, CPHA=0) or 1 (CPOL=1, CPHA=1) * Data sampled on first edge - 16-bit data frame - MSB first - ~{CS} pin active low - 25MHz clock



Board: 4 copper layers, 40.0 x 40.0 mm, 101 parts (18 on the bottom side), 62 nets.

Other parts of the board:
C37: 10uF/50V; C_0805_2012Metric

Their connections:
GND: C37.2; also elsewhere on the board
VBUS: C37.1; also elsewhere on the board

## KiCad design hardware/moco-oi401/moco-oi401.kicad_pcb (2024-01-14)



Board: 2 copper layers, 40.0 x 40.0 mm, 75 parts (13 on the bottom side), 48 nets.

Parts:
C1, C2: 1uF; C_0603_1608Metric
C3, C4, C5, C6, C9, C10: 100nF; C_0402_1005Metric
C7: 10nF; C_0402_1005Metric
C8: 1uF; C_0402_1005Metric
C11, C12: 12pF; C_0402_1005Metric
C13: 47nF/50V; C_0603_1608Metric
C14: 1uF/16V; C_0603_1608Metric
C15: 1uF/6.3V; C_0603_1608Metric
C16: 100nF/50V; C_0603_1608Metric
C17, C23, C24, C25, C26, C27, C28, C29, C30, C31, C32, C33: 10uF/50V; C_0805_2012Metric
C18: 100nF/6.3V; C_0603_1608Metric
C19: 22uF/16V; C_0805_2012Metric
C20, C21, C22: 22pF; C_0603_1608Metric
C34: 100nF; C_0603_1608Metric_Pad1.08x0.95mm_HandSolder
H1, H2, H3: MountingHole; MountingHole_2.2mm_M2_ISO14580
J1: Debug; PinHeader_2x04_P2.54mm_Vertical
J2: Serial; JST_GH_SM03B-GHS-TB_1x03-1MP_P1.25mm_Horizontal
J3: V+; wire_3.2mm
J4: V-; wire_3.2mm
J5: A; wire_3.2mm
J6: B; wire_3.2mm
J7: C; wire_3.2mm
L1: 47uH; L_Taiyo-Yuden_MD-3030
LD1: LED_BAGR; RGB LED 1.6x1.6mm
NT1: NetTie_2; NetTie-2_SMD_Pad0.5mm
R1, R3: 1k; R_0402_1005Metric
R2: 5.1k; R_0402_1005Metric
R4: 22R; R_0603_1608Metric
R5, R6: 5.1k; R_0603_1608Metric
R7, R8, R9: 330R; R_0603_1608Metric
R10: 10k/100mW; R_0603_1608Metric
R11, R12: 10k; R_0603_1608Metric
SB1, SB2: SolderJumper_2_Open; SolderJumper-2_P1.3mm_Open_RoundedPad1.0x1.5mm
SB3: SolderJumper_2_Bridged; SolderJumper-2_P1.3mm_Bridged_RoundedPad1.0x1.5mm
SW1: RESET; SW_SPST_CK_RS282G05A3
TP1: ~{RESET}; TestPoint_Pad_D1.0mm
TP2: V_{CC}; TestPoint_Pad_D1.0mm
TP3: GND; TestPoint_Pad_D1.0mm
TP4: V_{BK}; TestPoint_Pad_D1.0mm
TP5: PGND; TestPoint_Pad_D1.0mm
TP6: nSLEEP; TestPoint_Pad_D1.0mm
U1: RT9013-33GB; SOT-23-5
U2: STM32G431CBUx; QFN-48-1EP_7x7mm_P0.5mm_EP5.6x5.6mm
U3: DRV8316CR; VQFN-40_RGF_5x7mm_0.5mm_pitch_thermalpad
U4: LM4040A50; SOT-353_SC-70-5
U5: AS5047x; TSSOP-14_4.4x5mm_P0.65mm
Y1: 16MHz; Crystal_SMD_3225-4Pin_3.2x2.5mm

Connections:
+3.3V: C2.1, C3.1, C4.1, C5.1, C6.1, C7.1, C8.1, C34.2, J1.1, R5.1, R6.1, SB1.2 (B), SB3.2 (B), TP2.1, U1.5 (VOUT), U2.1 (VBAT), U2.21 (VDDA), U2.23 (VDD), U2.35 (VDD), U2.48 (VDD), U5.11 (VDD), U5.12 (VDD3V3)
+5V: C1.1, C19.2, J1.2, L1.2, LD1.2 (A), R4.2, SB1.1 (A), TP4.1, U1.1 (VIN), U1.3 (EN), U3.3 (FB_BK)
/ Rotary Sensor/MISO: R5.2, U2.42 (PB4), U3.33 (SDO), U5.3 (MISO)
/ Rotary Sensor/MOSI: U2.43 (PB5), U3.34 (SDI), U5.4 (MOSI)
/ Rotary Sensor/SCLK: U2.41 (PB3), U3.35 (SCLK), U5.2 (CLK)
/ Rotary Sensor/~CS: U2.19 (PB2), U5.1 (~CS)
/Driver/AVDD: C15.2, U3.25 (AVDD)
/Driver/DRVOFF: U2.25 (PB12), U3.21 (DRVOFF)
/Driver/INHA: U2.32 (PA10), U3.27 (INHA)
/Driver/INHB: U2.31 (PA9), U3.29 (INHB)
/Driver/INHC: U2.30 (PA8), U3.31 (INHC)
/Driver/INLA: U2.28 (PB15), U3.28 (INLA)
/Driver/INLB: U2.27 (PB14), U3.30 (INLB)
/Driver/INLC: U2.26 (PB13), U3.32 (INLC)
/Driver/OUTA: J5.1, U3.13 (OUTA), U3.14 (OUTA)
/Driver/OUTB: J6.1, U3.16 (OUTB), U3.17 (OUTB)
/Driver/OUTC: J7.1, U3.19 (OUTC), U3.20 (OUTC)
/Driver/SOA: C20.1, R7.1, U2.13 (PA5)
/Driver/SOB: C21.1, R8.1, U2.14 (PA6)
/Driver/SOC: C22.1, R9.1, U2.15 (PA7)
/Driver/V_{REF}: C9.1, C18.1, SB3.1 (A), U2.20 (VREF+), U3.37 (VREF/LILM)
/Driver/~CS: U2.47 (PB9), U3.36 (nSCS)
/Driver/~FAULT: R6.2, U2.24 (PB11), U3.22 (nFAULT)
/Driver/~SLEEP: R12.2, SB2.1 (A), TP6.1, U3.23 (nSLEEP)
/MCU/OSC_IN: C11.2, U2.5 (PF0), Y1.3
/MCU/OSC_OUT: C12.2, U2.6 (PF1), Y1.1
/SWCLK: J1.4, U2.37 (PA14)
/SWDIO: J1.6, U2.36 (PA13)
/UART1_RX: J1.3, J2.2, U2.45 (PB7)
/UART1_TX: J1.5, J2.1, U2.44 (PB6)
/USER_LED1: R1.2, U2.8 (PA0)
/USER_LED2: R3.2, U2.9 (PA1)
/~RESET: C10.1, SB2.2 (B), SW1.2, TP1.1, U2.7 (PG10)
GND: C1.2, C2.2, C3.2, C4.2, C5.2, C6.2, C7.2, C8.2, C9.2, C10.2, C11.1, C12.1, C15.1, C18.2, C19.1, C20.2, C21.2, C22.2, C34.1, J1.7, J1.8, J2.3, NT1.2, R2.2, SW1.1, TP3.1, U1.2 (GND), U2.49 (VSS), U3.2 (AGND), U3.4 (GND_BK), U3.26 (AGND), U3.41 (EP), U4.1 (A), U5.5 (TST), U5.13 (GND), Y1.2, Y1.4
GNDPWR: C16.1, C17.1, C23.2, C24.2, C25.2, C26.2, C27.2, C28.2, C29.2, C30.2, C31.2, C32.2, C33.2, J4.1, NT1.1, TP5.1, U3.12 (PGND), U3.15 (PGND), U3.18 (PGND)
unnamed: LD1.1 (BK), R3.1
unnamed: LD1.3 (GK), R2.1
unnamed: LD1.4 (RK), R1.1
unnamed: R11.2, R12.1
unnamed: C14.1, U3.8 (CP)
unnamed: C13.2, U3.7 (CPH)
unnamed: C13.1, U3.6 (CPL)
unnamed: R7.2, U3.40 (SOA)
unnamed: R8.2, U3.39 (SOB)
unnamed: R9.2, U3.38 (SOC)
unnamed: L1.1, R4.1, U3.5 (SW_BK)
unnamed: R10.2, R11.1, U4.3 (K)
Vdrive: C14.2, C16.2, C17.2, C23.1, C24.1, C25.1, C26.1, C27.1, C28.1, C29.1, C30.1, C31.1, C32.1, C33.1, J3.1, R10.1, U3.9 (VM), U3.10 (VM), U3.11 (VM)

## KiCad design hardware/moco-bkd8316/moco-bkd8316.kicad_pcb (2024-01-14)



Board: 2 copper layers, 35.5 x 41.0 mm, 50 parts (4 on the bottom side), 35 nets.

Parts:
C1: 47nF/50V; C_0603_1608Metric
C2: 1uF/16V; C_0603_1608Metric
C3: 1uF/6.3V; C_0603_1608Metric
C4: 100nF/50V; C_0603_1608Metric
C5, C11, C12, C13, C14, C15, C16, C17, C18: 10uF/50V; C_0805_2012Metric
C6: 100nF/6.3V; C_0603_1608Metric
C7: 22uF/16V; C_0805_2012Metric
C8, C9, C10: 22pF; C_0603_1608Metric
D1: LM4040A50; SOT-353_SC-70-5
H1, H2, H3, H4: MountingHole; MountingHole_3.2mm_M3
J1: Conn_02x10_Odd_Even; PinSocket_2x10_P2.54mm_Vertical
J2: Conn_01x02; PinHeader_1x02_P2.54mm_Vertical
J3, J4, J5: A; wire_3.2mm
J6: B; wire_3.2mm
J7: C; wire_3.2mm
L1: 47uH; L_Taiyo-Yuden_MD-3030
LD1: LED; LED_0805_2012Metric_Pad1.15x1.40mm_HandSolder
NT1: NetTie_2; NetTie-2_SMD_Pad0.5mm
R1: 22R; R_0603_1608Metric
R2, R3: 5.1k; R_0603_1608Metric
R4, R5, R6: 330R; R_0603_1608Metric
R7: 1.5k; R_0603_1608Metric
R8: 10k/100mW; R_0603_1608Metric
R9, R10: 10k; R_0603_1608Metric
SB1: SolderJumper_2_Open; SolderJumper-2_P1.3mm_Open_RoundedPad1.0x1.5mm
SW1: RESET; SW_SPST_CK_RS282G05A3
TP1, TP2, TP3: TestPoint; TestPoint_Pad_D1.5mm
TP4: nSLEEP; TestPoint_Pad_D1.0mm
U1: DRV8316CR; VQFN-40_RGF_5x7mm_0.5mm_pitch_thermalpad

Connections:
+3.3V: C3.2, J1.2, R2.1, R3.1, SB1.2 (B), TP1.1, U1.25 (AVDD)
/OUTA: J5.1, U1.13 (OUTA), U1.14 (OUTA)
/OUTB: J6.1, U1.16 (OUTB), U1.17 (OUTB)
/OUTC: J7.1, U1.19 (OUTC), U1.20 (OUTC)
DRVOFF: J1.4, U1.21 (DRVOFF)
GND: C3.1, C6.2, C7.1, C8.2, C9.2, C10.2, D1.1 (A), J1.19, J1.20, NT1.1, R7.2, SW1.1, TP3.1, U1.2 (AGND), U1.4 (GND_BK), U1.26 (AGND), U1.41 (EP)
GNDPWR: C4.1, C5.1, C11.2, C12.2, C13.2, C14.2, C15.2, C16.2, C17.2, C18.2, J2.2, J4.1, NT1.2, U1.12 (PGND), U1.15 (PGND), U1.18 (PGND)
MISO: J1.12, R2.2, U1.33 (SDO)
MOSI: J1.14, U1.34 (SDI)
unnamed: D1.3 (K), R8.2, R9.1
unnamed: LD1.1 (K), R7.1
unnamed: R9.2, R10.1
unnamed: C2.1, U1.8 (CP)
unnamed: C1.2, U1.7 (CPH)
unnamed: C1.1, U1.6 (CPL)
unnamed: R4.2, U1.40 (SOA)
unnamed: R5.2, U1.39 (SOB)
unnamed: R6.2, U1.38 (SOC)
unnamed: L1.1, R1.1, U1.5 (SW_BK)
PWM_H_A: J1.6, U1.27 (INHA)
PWM_H_B: J1.8, U1.29 (INHB)
PWM_H_C: J1.10, U1.31 (INHC)
PWM_L_A: J1.5, U1.28 (INLA)
PWM_L_B: J1.7, U1.30 (INLB)
PWM_L_C: J1.9, U1.32 (INLC)
SCLK: J1.16, U1.35 (SCLK)
SOA: C8.1, J1.17, R4.1
SOB: C9.1, J1.15, R5.1
SOC: C10.1, J1.13, R6.1
VBUS: C2.2, C4.2, C5.2, C11.1, C12.1, C13.1, C14.1, C15.1, C16.1, C17.1, C18.1, J2.1, J3.1, R8.1, U1.9 (VM), U1.10 (VM), U1.11 (VM)
VCC: C7.2, J1.1, L1.2, LD1.2 (A), R1.2, TP2.1, U1.3 (FB_BK)
VREF: C6.1, J1.11, SB1.1 (A), U1.37 (VREF/LILM)
~CS: J1.18, U1.36 (nSCS)
~FAULT: J1.3, R3.2, U1.22 (nFAULT)
~SLEEP: R10.2, SW1.2, TP4.1, U1.23 (nSLEEP)

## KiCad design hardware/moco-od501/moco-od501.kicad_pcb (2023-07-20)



Board: 4 copper layers, 60.0 x 60.0 mm, 102 parts (13 on the bottom side), 71 nets.

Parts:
C1, C10, C21, C22, C23, C24, C28, C29, C32: 100nF; C_0402_1005Metric
C2: 1uF/50V; C_1206_3216Metric
C3, C9: 10uF; C_0603_1608Metric
C4, C5, C26, C27: 1uF; C_0402_1005Metric
C6: 1uF/6.3V; C_0402_1005Metric
C7: 100nF/6.3V; C_0402_1005Metric
C8: 47nF; C_0603_1608Metric
C11: 1uF/16V; C_0603_1608Metric
C12, C13, C14, C15, C16, C17, C18, C19, C20: 10uF/50V; C_1206_3216Metric
C25: 10nF; C_0402_1005Metric
C30, C31: 12pF; C_0402_1005Metric
C33, C34: 30pF; C_0402_1005Metric
C35: 100nF; C_0603_1608Metric_Pad1.08x0.95mm_HandSolder
C36: 1uF; C_0603_1608Metric_Pad1.08x0.95mm_HandSolder
C37, C38, C39, C40, C41, C42, C43, C44, C45: 10uF/50V; C_1206_3216Metric_Pad1.33x1.80mm_HandSolder
D1: SS34; D_SMA
H1, H2, H3: MountingHole; MountingHole_3.2mm_M3_ISO14580
J1: Serial; JST_GH_BM03B-GHS-TBT_1x03-1MP_P1.25mm_Vertical
J2: Debug; PinHeader_2x04_P2.54mm_Vertical
J3, J4, J5: A; wire_3.2mm
J6: B; wire_3.2mm
J7: C; wire_3.2mm
J8: CAN1; JST_GH_BM02B-GHS-TBT_1x02-1MP_P1.25mm_Vertical
J9: CAN2; JST_GH_BM02B-GHS-TBT_1x02-1MP_P1.25mm_Vertical
L1: 22uH; L_7.3x7.3_H3.5
LD1: LED_BAGR; RGB LED 1.6x1.6mm
NT1, NT2, NT3, NT4, NT5, NT6, NT7: NetTie_2; NetTie-2_SMD_Pad0.5mm
Q1, Q2, Q3, Q4, Q5, Q6: CSD18540Q5B; TDSON-8-1
R1: 54.9k; R_0402_1005Metric
R2, R3, R10: 10k; R_0402_1005Metric
R4, R6: 1k; R_0402_1005Metric
R5: 5k; R_0402_1005Metric
R7, R8, R9: 0.5mΩ; R_2512_6332Metric
R11, R14, R15, R18: DNI; R_0402_1005Metric_Pad0.72x0.64mm_HandSolder
R12, R13, R16: 0R; R_0402_1005Metric_Pad0.72x0.64mm_HandSolder
R17: 47k; R_0402_1005Metric_Pad0.72x0.64mm_HandSolder
R19: 120R; R_0402_1005Metric
SB1: SolderJumper_3_Bridged12; SolderJumper-3_P1.3mm_Bridged12_RoundedPad1.0x1.5mm
SW1: RESET; SW_SPST_TL3342
TH1: NCP18XH103F03RB; R_0603_1608Metric
U1: LMR16006X; SOT-23-6
U2: RT9013-33GB; SOT-23-5
U3: DRV8323H; QFN-40-1EP_6x6mm_P0.5mm_EP4.6x4.6mm_ThermalVias
U4: STM32G431CBUx; QFN-48-1EP_7x7mm_P0.5mm_EP5.6x5.6mm
U5: TJA1050; SOIC-8_3.9x4.9mm_P1.27mm
U6: AS5047x; TSSOP-14_4.4x5mm_P0.65mm
Y1: 8MHz; Crystal_SMD_3225-4Pin_3.2x2.5mm

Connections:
+3.3V: C5.1, C21.1, C22.1, C23.1, C24.1, C25.1, C26.1, C35.1, C36.1, J2.1, R10.1, SB1.1 (A), TH1.1, U2.5 (VOUT), U4.1 (VBAT), U4.21 (VDDA), U4.23 (VDD), U4.35 (VDD), U4.48 (VDD), U6.11 (VDD), U6.12 (VDD3V3)
+5V: C3.1, C4.1, C32.2, J2.2, L1.2, LD1.2 (A), R1.1, U2.1 (VIN), U2.3 (CE), U5.3 (VCC)
/CAN Bus/CAN_H: C33.1, J8.1, J9.1, R19.1, U5.7 (CANH)
/CAN Bus/CAN_L: C34.1, J8.2, J9.2, R19.2, U5.6 (CANL)
/CAN_RX: U4.33 (PA11), U5.4 (RXD)
/CAN_TX: U4.34 (PA12), U5.1 (TXD)
/MCU/AMP_CAL: U3.31 (CAL), U4.39 (PC10)
/MCU/CS_A: U3.23 (SOA), U4.13 (PA5)
/MCU/CS_B: U3.22 (SOB), U4.14 (PA6)
/MCU/CS_C: U3.21 (SOC), U4.15 (PA7)
/MCU/GATE_ENABLE: U3.30 (ENABLE), U4.29 (PC6)
/MCU/OSC_IN: C30.2, U4.5 (PF0), Y1.3
/MCU/OSC_OUT: C31.2, U4.6 (PF1), Y1.1
/MCU/PWM_HA: U3.34 (INHA), U4.30 (PA8)
/MCU/PWM_HB: U3.36 (INHB), U4.31 (PA9)
/MCU/PWM_HC: U3.38 (INHC), U4.32 (PA10)
/MCU/PWM_LA: U3.35 (INLA), U4.26 (PB13)
/MCU/PWM_LB: U3.37 (INLB), U4.27 (PB14)
/MCU/PWM_LC: U3.39 (INLC), U4.28 (PB15)
/MCU/VREF: C7.2, SB1.3 (B), U3.24 (VREF)
/MCU/~FAULT: R10.2, U3.25 (nFAULT), U4.16 (PC4)
/Motor Driver/GAIN: R15.2, R17.1, U3.29 (GAIN)
/Motor Driver/GHA: Q1.4 (G), U3.6 (GHA)
/Motor Driver/GHB: Q2.4 (G), U3.15 (GHB)
/Motor Driver/GHC: Q3.4 (G), U3.16 (GHC)
/Motor Driver/GLA: Q4.4 (G), U3.8 (GLA)
/Motor Driver/GLB: Q5.4 (G), U3.13 (GLB)
/Motor Driver/GLC: Q6.4 (G), U3.18 (GLC)
/Motor Driver/IDRIVE: R12.2, R14.1, U3.27 (IDRIVE)
/Motor Driver/MODE: R11.2, R13.1, U3.26 (MODE)
/Motor Driver/OUTA: J5.1, Q1.1 (S), Q1.2 (S), Q1.3 (S), Q4.5 (D), U3.7 (SHA)
/Motor Driver/OUTB: J6.1, Q2.1 (S), Q2.2 (S), Q2.3 (S), Q5.5 (D), U3.14 (SHB)
/Motor Driver/OUTC: J7.1, Q3.1 (S), Q3.2 (S), Q3.3 (S), Q6.5 (D), U3.17 (SHC)
/Motor Driver/SNA: NT4.1, U3.10 (SNA)
/Motor Driver/SNB: NT5.1, U3.11 (SNB)
/Motor Driver/SNC: NT6.1, U3.20 (SNC)
/Motor Driver/SPA: NT1.1, U3.9 (SPA)
/Motor Driver/SPB: NT2.1, U3.12 (SPB)
/Motor Driver/SPC: NT3.1, U3.19 (SPC)
/Motor Driver/VDS: R16.2, R18.1, U3.28 (VDS)
/SPI_MISO: U4.42 (PB4), U6.3 (MISO)
/SPI_MOSI: U4.43 (PB5), U6.4 (MOSI)
/SPI_SCLK: U4.41 (PB3), U6.2 (CLK)
/SPI_~CS_AS5047: U4.19 (PB2), U6.1 (~CS)
/SWCLK: J2.4, U4.37 (PA14)
/SWDIO: J2.6, U4.36 (PA13)
/TEMP_SENSOR: R2.2, TH1.2, U4.25 (PB12)
/UART1_RX: J2.5, U4.45 (PB7)
/UART1_TX: J2.3, U4.44 (PB6)
/UART2_RX: J1.2, U4.11 (PA3)
/UART2_TX: J1.1, U4.10 (PA2)
/USER_LED1: R4.2, U4.17 (PB0)
/USER_LED2: R6.2, U4.18 (PB1)
/~RESET: C29.1, SW1.2, U4.7 (PG10)
GND: C2.2, C3.2, C4.2, C5.2, C6.1, C7.1, C9.1, C10.1, C12.2, C13.2, C14.2, C15.2, C16.2, C17.2, C18.2, C19.2, C20.2, C21.2, C22.2, C23.2, C24.2, C25.2, C26.2, C27.2, C28.2, C29.2, C30.1, C31.1, C32.1, C33.2, C34.2, C35.2, C36.2, C37.2, C38.2, C39.2, C40.2, C41.2, C42.2, C43.2, C44.2, C45.2, D1.2 (A), J1.3, J2.7, J2.8, J4.1, NT4.2, NT5.2, NT6.2, R2.1, R3.2, R5.2, R7.2, R8.2, R9.2, R13.2, R14.2, R17.2, R18.2, SW1.1, U1.2 (GND), U2.2 (GND), U3.32 (AGND), U3.40 (PGND), U3.41 (GND), U4.49 (VSS), U5.2 (GND), U5.8 (S), U6.5 (TST), U6.13 (GND), Y1.2, Y1.4
unnamed: C1.2, D1.1 (K), L1.1, U1.6 (SW)
unnamed: LD1.1 (BK), R6.1
unnamed: LD1.3 (GK), R5.1
unnamed: LD1.4 (RK), R4.1
unnamed: NT1.2, Q4.1 (S), Q4.2 (S), Q4.3 (S), R7.1
unnamed: NT2.2, Q5.1 (S), Q5.2 (S), Q5.3 (S), R8.1
unnamed: NT3.2, Q6.1 (S), Q6.2 (S), Q6.3 (S), R9.1
unnamed: C27.1, C28.1, SB1.2 (C), U4.20 (VREF+)
unnamed: C1.1, U1.1 (CB)
unnamed: R1.2, R3.1, U1.3 (FB)
unnamed: C8.1, U3.2 (CPH)
unnamed: C8.2, U3.1 (CPL)
unnamed: C11.1, U3.3 (VCP)
unnamed: NT7.2, U3.5 (VDRAIN)
VDD: C6.2, R11.1, R12.1, R15.1, R16.1, U3.33 (DVDD)
Vdrive: C2.1, C9.2, C10.2, C11.2, C12.1, C13.1, C14.1, C15.1, C16.1, C17.1, C18.1, C19.1, C20.1, C37.1, C38.1, C39.1, C40.1, C41.1, C42.1, C43.1, C44.1, C45.1, J3.1, NT7.1, Q1.5 (D), Q2.5 (D), Q3.5 (D), U1.5 (VIN), U3.4 (VM)

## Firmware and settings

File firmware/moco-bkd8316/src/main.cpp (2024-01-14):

/**
 * @file   main.cpp
 * @brief  SimpleFOC BLDC driver firmware for moco-BKD8316 (a DRV8316 breakout board).
 * @author ZiTe (honmonoh@gmail.com)
 * @note   Ref: https://github.com/simplefoc/Arduino-FOC-drivers/tree/master/examples/drivers/drv8316
 */

#define SERIAL_UART_INSTANCE (2)

#include <Arduino.h>
#include <Wire.h>
#include <SimpleFOC.h>
#include <SimpleFOCDrivers.h>
#include "drivers/drv8316/drv8316.h"

/* Motor selection. */
// #define T_MOTOR_U8
// #define T_MOTOR_U10II
#define QM4208

// #define PWM_MODE_3 /* Comment out to use 6x PWM mode. */
#define OPENLOOP   /* Comment out to use close-loop control. */
// #define ANGLE_CONTROL /* Comment out to use velocity control. */

#define BAUDRATE (115200) /* Serial port baudrate. */
#define DEFAULT_TARGET (10)

/* Motor parameters. */
#if defined(T_MOTOR_U8)
  #define MOTOR_POLE_PAIRS (21)
  #define MOTOR_PHASE_RESISTANCE (NOT_SET) /* Unit in ohm. */
  #define MOTOR_KV (135)                   /* Unit in rpm/V. */
#elif defined(T_MOTOR_U10II)
  #define MOTOR_POLE_PAIRS (21)
  #define MOTOR_PHASE_RESISTANCE (NOT_SET) /* Unit in ohm. */
  #define MOTOR_KV (100)                   /* Unit in rpm/V. */
#elif defined(QM4208)
  #define MOTOR_POLE_PAIRS (7)
  #define MOTOR_PHASE_RESISTANCE (NOT_SET) /* Unit in ohm. */
  #define MOTOR_KV (380)                   /* Unit in rpm/V. */
#else
  #error No Motor Selected
#endif

/*
 * Pinmap.
 *
 * Select board/MCU by PlatformIO env (platformio.ini).
 * Arduino SPI:
 * - SCLK: D13.
 * - MISO: D12.
 * - MOSI: D11.
 */
#if defined(NUCLEO_F446RE) || defined(NUCLEO_F401RE)
  #define PWMH_A (PA8)  /* TIM1_CH1. */
  #define PWMH_B (PA9)  /* TIM1_CH2. */
  #define PWMH_C (PA10) /* TIM1_CH3. */

  #define PWML_A (PB13) /* TIM1_CH1N. */
  #define PWML_B (PB14) /* TIM1_CH2N. */
  #define PWML_C (PB15) /* TIM1_CH3N. */

  #define DRIVER_SPI_CS (PB6)
  #define DRIVER_FAULT (PB8)
#elif defined(NUCLEO_L432KC)
  #error
#else
  #error No Board Selected
#endif

/* Power. */
#define VOLTAGE_SUPPLY (6 * 3.7) /* Unit in V. */
#define CURRENT_LIMIT (1)      /* Unit in A. */

BLDCMotor motor = BLDCMotor(MOTOR_POLE_PAIRS);

#ifdef PWM_MODE_3
DRV8316Driver3PWM driver = DRV8316Driver3PWM(PWMH_A, PWMH_B, PWMH_C, DRIVER_SPI_CS, false, NOT_SET, DRIVER_FAULT);
#else
DRV8316Driver6PWM driver = DRV8316Driver6PWM(PWMH_A, PWML_A, PWMH_B, PWML_B, PWMH_C, PWML_C, DRIVER_SPI_CS, false, NOT_SET, DRIVER_FAULT);
#endif

HardwareSerial Serial1(USART1); /* Change Serial instance from platformio.ini. */
Commander command = Commander(Serial);
void onMotor(char *cmd) { command.motor(&motor, cmd); }

void printDRV8316Status(void);
void setup()
{
  /* Communication setup. https://docs.simplefoc.com/commander_interface */
  Serial.begin(BAUDRATE);
  motor.useMonitoring(Serial);
  command.add('M', onMotor, "motor");

  // pinMode(PWMH_A, OUTPUT);
  // digitalWrite(PWMH_A, 1);
  // pinMode(PWMH_B, OUTPUT);
  // digitalWrite(PWMH_B, 1);
  // pinMode(PWMH_C, OUTPUT);
  // digitalWrite(PWMH_C, 1);

#ifndef OPENLOOP
  /* Configure angle/Position sensor. https://docs.simplefoc.com/magnetic_sensor_spi */
  angleSensor.spi_mode = SPI_MODE1; /* CPOL=0, CPHA=1. */
  angleSensor.clock_speed = 1e6;    /* 10 MHz max. */
  angleSensor.init();
  motor.linkSensor(&angleSensor);
#endif

  /* Configure driver. https://github.com/simplefoc/Arduino-FOC-drivers/tree/master/examples/drivers/drv8316 */
  driver.voltage_power_supply = VOLTAGE_SUPPLY;
driver.pwm_frequency = 2e4;
#ifndef PWM_MODE_3
  // driver.dead_zone = 0.05;
#endif
  driver.init();
  motor.linkDriver(&driver);

  /* Configure motor parameters. https://docs.simplefoc.com/bldcmotor */
  // motor.phase_resistance = MOTOR_PHASE_RESISTANCE;
  // motor.KV_rating = MOTOR_KV * 1.5; /* SimpleFOC suggest to set the KV value provided to the library to 50-70% higher than the one given in the datasheet.. */
  motor.voltage_limit = VOLTAGE_SUPPLY * 0.17;
  motor.current_limit = CURRENT_LIMIT;
  // motor.motion_downsample = 5;

  /* Algorithms and controllers setup. */
  // motor.foc_modulation = FOCModulationType::SpaceVectorPWM;
  // motor.torque_controller = TorqueControlType::voltage;
#if defined(OPENLOOP) && defined(ANGLE_CONTROL)
  motor.controller = MotionControlType::angle_openloop;
#elif defined(OPENLOOP) && !defined(ANGLE_CONTROL)
  motor.controller = MotionControlType::velocity_openloop;
#elif !defined(OPENLOOP) && defined(ANGLE_CONTROL)
  motor.controller = MotionControlType::angle;
#elif !defined(OPENLOOP) && !defined(ANGLE_CONTROL)
  motor.controller = MotionControlType::velocity;
#endif

  /* Velocity control loop setup. */
  // motor.PID_velocity.P = 0.2;
  // motor.PID_velocity.I = 20;
  // motor.PID_velocity.D = 0.001;
  // motor.PID_velocity.output_ramp = 500; /* Unit in volts/s. */
  motor.LPF_velocity.Tf = 0.01;
  // motor.velocity_limit = 15; /* Unit in rad/s. */

  /* Angle/Position control loop setup. */
  // motor.P_angle.P = 5;
  // motor.P_angle.I = 0.5;
  // motor.P_angle.D = 0.0;
  // motor.P_angle.output_ramp = 500; /* Acceleration limit(?), unit in rad/s^2. */

  motor.init(); /* Initialize motor. */
  // motor.initFOC(); /* Start FOC and aligh encoder. */

#ifndef OPENLOOP
  angleSensor.update();
  motor.target = angleSensor.getAngle(); /* Set the initial target value. */
#else
  motor.target = DEFAULT_TARGET;
#endif

  Serial.println(motor.target, 3);

  Serial.println("All Ready!");
  _delay(1000);
  driver.clearFault();
  printDRV8316Status();
  // motor.enable();
  // driver.setDriverOffEnabled(true);
  driver.setDriverOffEnabled(false);
  // driver.enable();
}

void loop()
{
  driver.clearFault();
  // motor.loopFOC(); /* Main FOC algorithm. */
  motor.move(DEFAULT_TARGET); /* Motion control. */

  driver.clearFault();
  command.run();
}

void printDRV8316Status(void)
{
  DRV8316Status status = driver.getStatus();
  Serial.println("DRV8316 Status:");
  Serial.print("Fault: ");
  Serial.println(status.isFault());
  Serial.print("Buck Error: ");
  Serial.print(status.isBuckError());
  Serial.print("  Undervoltage: ");
  Serial.print(status.isBuckUnderVoltage());
  Serial.print("  OverCurrent: ");
  Serial.println(status.isBuckOverCurrent());
  Serial.print("Charge Pump UnderVoltage: ");
  Serial.println(status.isChargePumpUnderVoltage());
  Serial.print("OTP Error: ");
  Serial.println(status.isOneTimeProgrammingError());
  Serial.print("OverCurrent: ");
  Serial.print(status.isOverCurrent());
  Serial.print("  Ah: ");
  Serial.print(status.isOverCurrent_Ah());
  Serial.print("  Al: ");
  Serial.print(status.isOverCurrent_Al());
  Serial.print("  Bh: ");
  Serial.print(status.isOverCurrent_Bh());
  Serial.print("  Bl: ");
  Serial.print(status.isOverCurrent_Bl());
  Serial.print("  Ch: ");
  Serial.print(status.isOverCurrent_Ch());
  Serial.print("  Cl: ");
  Serial.println(status.isOverCurrent_Cl());
  Serial.print("OverTemperature: ");
  Serial.print(status.isOverTemperature());
  Serial.print("  Shutdown: ");
  Serial.print(status.isOverTemperatureShutdown());
  Serial.print("  Warning: ");
  Serial.println(status.isOverTemperatureWarning());
  Serial.print("OverVoltage: ");
  Serial.println(status.isOverVoltage());
  Serial.print("PowerOnReset: ");
  Serial.println(status.isPowerOnReset());
  Serial.print("SPI Error: ");
  Serial.print(status.isSPIError());
  Serial.print("  Address: ");
  Serial.print(status.isSPIAddressError());
  Serial.print("  Clock: ");
  Serial.print(status.isSPIClockFramingError());
  Serial.print("  Parity: ");
  Serial.println(status.isSPIParityError());
  if (status.isFault())
    driver.clearFault();
  delayMicroseconds(1); // ensure 400ns delay
  DRV8316_PWMMode val = driver.getPWMMode();
  Serial.print("PWM Mode: ");
  Serial.println(val);
  delayMicroseconds(1); // ensure 400ns delay
  bool lock = driver.isRegistersLocked();
  Serial.print("Lock: ");
  Serial.println(lock);
}

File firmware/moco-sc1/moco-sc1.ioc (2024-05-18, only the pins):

Mcu.UserName=STM32G431VBTx
PA0.Signal=S_TIM2_CH1
PA1.GPIO_Label=OPA1_P
PA1.Signal=OPAMP1_VINP
PA10.GPIO_Label=UART_RX
PA10.Signal=USART1_RX
PA11.GPIO_Label=CAN_RX
PA11.Signal=FDCAN1_RX
PA12.GPIO_Label=CAN_TX
PA12.Signal=FDCAN1_TX
PA13.GPIO_Label=SWDIO
PA13.Signal=SYS_JTMS-SWDIO
PA14.GPIO_Label=SWCLK
PA14.Signal=SYS_JTCK-SWCLK
PA15.Signal=GPIO_Output
PA2.GPIO_Label=OPA1_O
PA2.Signal=SharedAnalog_PA2
PA3.GPIO_Label=OPA1_M
PA3.Signal=OPAMP1_VINM
PA4.GPIO_Label=VBUS_SENSE
PA4.Signal=ADC2_IN17
PA6.GPIO_Label=OPA2_O
PA6.Signal=SharedAnalog_PA6
PA7.GPIO_Label=OPA2_P
PA7.Signal=OPAMP2_VINP
PA9.GPIO_Label=UART_TX
PA9.Signal=USART1_TX
PB0.GPIO_Label=OPA3_P
PB0.Signal=OPAMP3_VINP
PB1.GPIO_Label=OPA3_O
PB1.Signal=SharedAnalog_PB1
PB2.GPIO_Label=OPA3_M
PB2.Signal=OPAMP3_VINM
PB3.Signal=SPI3_SCK
PB4.GPIO_Label=ENC_SPI_MISO
PB4.Signal=SPI1_MISO
PB5.GPIO_Label=ENC_SPI_MOSI
PB5.Signal=SPI1_MOSI
PB6.GPIO_Label=ENC_SPI_nCS
PB6.Signal=GPIO_Output
PC5.GPIO_Label=OPA2_M
PC5.Signal=OPAMP2_VINM
PC8.GPIO_Label=GD_SCL
PC8.Signal=I2C3_SCL
PC9.GPIO_Label=GD_SDA
PC9.Signal=I2C3_SDA
PE10.GPIO_Label=GD_INL2
PE10.Signal=TIM1_CH2N
PE11.GPIO_Label=GD_INH2
PE11.Signal=S_TIM1_CH2
PE12.GPIO_Label=GD_INL3
PE12.Signal=TIM1_CH3N
PE13.GPIO_Label=GD_INH3
PE13.Signal=S_TIM1_CH3
PE14.GPIO_Label=GD_READY
PE14.Signal=GPIO_Input
PE15.Signal=GPIO_Input
PE7.GPIO_Label=GD_WAKE
PE7.Signal=GPIO_Output
PE8.GPIO_Label=GD_INL1
PE8.Signal=TIM1_CH1N
PE9.GPIO_Label=GD_INH1
PE9.Signal=S_TIM1_CH1
PF0-OSC_IN.Signal=RCC_OSC_IN
PF1-OSC_OUT.Signal=RCC_OSC_OUT

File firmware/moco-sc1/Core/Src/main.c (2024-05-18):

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
/* Includes ------------------------------------------------------------------*/
#include "main.h"

/* USER CODE BEGIN Includes */
#include "stspin32g4_gate_driver.h"
#include "heartbeat.h"
#include "stspin32g4.h"
/* USER CODE END Includes */


FDCAN_HandleTypeDef hfdcan1;

OPAMP_HandleTypeDef hopamp1;
OPAMP_HandleTypeDef hopamp2;
OPAMP_HandleTypeDef hopamp3;

void SystemClock_Config(void);
static void MX_GPIO_Init(void);
static void MX_ADC2_Init(void);
static void MX_FDCAN1_Init(void);
static void MX_I2C3_Init(void);
static void MX_OPAMP1_Init(void);
static void MX_OPAMP2_Init(void);
static void MX_OPAMP3_Init(void);
static void MX_TIM1_Init(void);
static void MX_TIM16_Init(void);
static void MX_USART1_UART_Init(void);
static void MX_TIM2_Init(void);
static void MX_TIM8_Init(void);
static void MX_TIM3_Init(void);
static void MX_ADC1_Init(void);
/* USER CODE BEGIN 0 */
extern float act;
/* USER CODE END 0 */

/**
  * @brief  The application entry point.
  * @retval int
  */
int main(void)
{
  /* MCU Configuration--------------------------------------------------------*/

  /* Reset of all peripherals, Initializes the Flash interface and the Systick. */
  HAL_Init();

  /* Configure the system clock */
  SystemClock_Config();

  /* Initialize all configured peripherals */
  MX_GPIO_Init();
  MX_ADC2_Init();
  MX_FDCAN1_Init();
  MX_I2C3_Init();
  MX_OPAMP1_Init();
  MX_OPAMP2_Init();
  MX_OPAMP3_Init();
  MX_TIM1_Init();
  MX_TIM16_Init();
  MX_USART1_UART_Init();
  MX_TIM2_Init();
  MX_TIM8_Init();
  MX_TIM3_Init();
  MX_ADC1_Init();
  /* USER CODE BEGIN 2 */
  heartbeat_init();
  spg4_init();
  gd_init();
  /* USER CODE END 2 */

  /* Infinite loop */
  /* USER CODE BEGIN WHILE */
  LL_USART_TransmitData8(USART1, 0x41);
  while (1)
  {
    /* USER CODE END WHILE */

    /* USER CODE BEGIN 3 */
    LL_USART_TransmitData8(USART1, act);
    LL_USART_TransmitData8(USART1, 0xFE);
    gd_clear_fault();

    //LL_USART_TransmitData8(USART1, (uint8_t)vbus_adc);

    //spg4_set_pwm(60, 0, 0);
    HAL_Delay(500);
  }
  /* USER CODE END 3 */
}

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


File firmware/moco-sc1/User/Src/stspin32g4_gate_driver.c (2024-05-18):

#include "main.h"
#include "cmsis_compiler.h"
#include "stm32g4xx_ll_i2c.h"
#include "stm32g4xx_ll_gpio.h"
#include "stspin32g4_gate_driver.h"

#define GD_I2C_INST (I2C3)
#define GD_ADDRESS (0x8EU) // 1000111Xb, x:R/W

#define GD_REG_POWMNG (0x01U)
#define GD_REG_LOGIC (0x02U)
#define GD_REG_READY (0x07U)
#define GD_REG_NFAULT (0x08U)
#define GD_REG_CLEAR (0x09U)
#define GD_REG_STBY (0x0AU)
#define GD_REG_LOCK (0x0BU)
#define GD_REG_RESET (0x0CU)
#define GD_REG_STATUS (0x80U)

/**
 * @note Protected
 */
typedef __PACKED_UNION
{
    __PACKED_STRUCT
    {
        uint8_t vcc_val : 2;
        const uint8_t _reserved23 : 2; // Unused, default=0b00
        uint8_t stby_reg_en : 1;
        uint8_t vcc_dis : 1;
        uint8_t reg3v3_dis : 1;
        const uint8_t _reserved7 : 1; // Unused, default=0b0
    }
    bit;
    uint8_t reg;
}
reg_powmng_t;

/**
 * @note Protected
 */
typedef __PACKED_UNION
{
    __PACKED_STRUCT
    {
        uint8_t ilock : 1;
        uint8_t dtmin : 1;
        uint8_t vds_p_deg : 2;
        const uint8_t _reserved47 : 4; // Unused, default=0x0111
    }
    bit;
    uint8_t reg;
}
reg_logic_t;

typedef __PACKED_UNION
{
    __PACKED_STRUCT
    {
        uint8_t vcc_uvlo_rdy : 1;
        uint8_t thsd_rdy : 1;
        const uint8_t _reserved2 : 1; // Unused, default=0b0
        uint8_t stby_rdy : 1;
        const uint8_t _reserved47 : 4; // Unused, default=0b0000
    }
    bit;
    uint8_t reg;
}
reg_ready_t;

/**
 * @note Protected
 */
typedef __PACKED_UNION
{
    __PACKED_STRUCT
    {
        uint8_t vcc_uvlo_flt : 1;
        uint8_t thsd_flt : 1;
        uint8_t vds_p_flt : 1;
        const uint8_t _reserved37 : 5; // Unused, default=0b01111
    }
    bit;
    uint8_t reg;
}
reg_nfault_t;

typedef __PACKED_UNION
{
    __PACKED_STRUCT
    {
        uint8_t fault_clear : 8;
    }
    bit;
    uint8_t reg;
}
reg_clear_t;

/**
 * @note Protected
 */
typedef __PACKED_UNION
{
    __PACKED_STRUCT
    {
        uint8_t stby : 1;
        const uint8_t _reserved27 : 7; // Unused, default=0b0000000
    }
    bit;
    uint8_t reg;
}
reg_stby_t;

typedef __PACKED_UNION
{
    __PACKED_STRUCT
    {
        uint8_t lock : 4;
        uint8_t nlock : 4;
    }
    bit;
    uint8_t reg;
}
reg_lock_t;

/**
 * @note Protected
 */
typedef __PACKED_UNION
{
    __PACKED_STRUCT
    {
        uint8_t reset : 8;
    }
    bit;
    uint8_t reg;
}
reg_reset_t;

/**
 * @note Ready only
 */
typedef __PACKED_UNION
{
    __PACKED_STRUCT
    {
        uint8_t vcc_uvlo : 1;
        uint8_t thsd : 1;
        uint8_t vds_p : 1;
        uint8_t reset : 1;
        const uint8_t _reserved46 : 3; // Unused
        uint8_t lock : 1;
    }
    bit;
    uint8_t reg;
}
reg_status_t;

int8_t i2c_send_blocking(const uint8_t *data, uint8_t len);
uint8_t i2c_read_blocking(uint8_t addr);

reg_powmng_t reg_powmng = {
    .bit.vcc_val = 0,
    .bit._reserved23 = 0,
    .bit.stby_reg_en = 0,
    .bit.vcc_dis = 0,
    .bit.reg3v3_dis = 0,
    .bit._reserved7 = 0,
};

reg_logic_t reg_logic = {
    .bit.ilock = 1,
    .bit.dtmin = 1,
    .bit.vds_p_deg = 0,
    .bit._reserved47 = 0x7,
};

reg_ready_t reg_ready = {
    .bit.vcc_uvlo_rdy = 1,
    .bit.thsd_rdy = 0,
    .bit._reserved2 = 0,
    .bit.stby_rdy = 1,
    .bit._reserved47 = 0,
};

reg_nfault_t reg_nfault = {
    .reg = 0x7F,
};

/**
 * @brief Clear all faults
 */
void gd_clear_fault(void)
{
    const reg_clear_t reg_clear = {.bit.fault_clear = 0xFF};
    uint8_t data[] = {GD_REG_CLEAR, reg_clear.reg};
    i2c_send_blocking(data, 2);
}

/**
 * @brief Unlock to write protected registers, and all gate driver output are forced low.
 */
void gd_unlock(void)
{
    // LOCK!=NLOCK: protected registers unlock.
    const reg_lock_t reg_unlock = {
        .bit.nlock = 0xF,
        .bit.lock = 0x0,
    };
    uint8_t data[] = {GD_REG_LOCK, reg_unlock.reg};
    i2c_send_blocking(data, 2);
}

/**
 * @brief Lock protected registers.
 */
void gd_lock(void)
{
    // LOCK==NLOCK: protected registers lock.
    const reg_lock_t reg_lock = {
        .bit.nlock = 0x0,
        .bit.lock = 0x0,
    };
    uint8_t data[] = {GD_REG_LOCK, reg_lock.reg};
    i2c_send_blocking(data, 2);
}

/**
 * @brief Enter low consumption mode. Need to unlock.
 */
void gd_enter_standby(void)
{
    const reg_stby_t reg_stby = {
        .bit.stby = 1,
        .bit._reserved27 = 0x00,
    };
    uint8_t data[] = {GD_REG_STBY, reg_stby.reg};
    i2c_send_blocking(data, 2);
}

/**
 * @brief Reset registers to the default value. Need to unlock.
 */
void gd_reset(void)
{
    // Setting high all the bits resets the regs to the default value.
    const reg_reset_t reg_reset = {.bit.reset = 0xFF};
    uint8_t data[] = {GD_REG_RESET, reg_reset.reg};
    i2c_send_blocking(data, 2);
}

/**
 * @brief Wake-up
 */
void gd_wakeup(void)
{
    LL_GPIO_SetOutputPin(GD_WAKE_GPIO_Port, GD_WAKE_Pin);
    HAL_Delay(50);
    LL_GPIO_ResetOutputPin(GD_WAKE_GPIO_Port, GD_WAKE_Pin);
}

uint8_t gd_init(void)
{
    gd_wakeup();
    HAL_Delay(2);

    gd_clear_fault();
    HAL_Delay(2);

    gd_unlock();
    HAL_Delay(2);

    gd_reset();
    HAL_Delay(2);

    // uint8_t data[2] = {0};

    // Setup power manager config
    // reg_powmng.bit.vcc_val = 0;
    // reg_powmng.bit.stby_reg_en = 0;
    // reg_powmng.bit.vcc_dis = 1;
    // reg_powmng.bit.reg3v3_dis = 1;
    // data[0] = GD_REG_POWMNG;
    // data[1] = reg_powmng.reg;
    // i2c_send_blocking(data, 2);

    // Setup driving logic config
    // reg_logic.bit.ilock = 1;
    // reg_logic.bit.dtmin = 1;
    // reg_logic.bit.vds_p_deg = 0;
    // data[0] = GD_REG_LOGIC;
    // data[1] = reg_logic.reg;
    // i2c_send_blocking(data, 2);

    gd_lock();
    HAL_Delay(2);

    return (uint8_t)i2c_read_blocking(GD_REG_STATUS);
}

uint8_t get_status(void)
{
    return i2c_read_blocking(GD_REG_STATUS);
}

int8_t i2c_send_blocking(const uint8_t *data, uint8_t len)
{
    LL_I2C_HandleTransfer(GD_I2C_INST,
                          GD_ADDRESS,
                          LL_I2C_ADDRSLAVE_7BIT,
                          len,
                          LL_I2C_MODE_AUTOEND,
                          LL_I2C_GENERATE_START_WRITE);
    for (uint8_t i = 0; i < len; i++)
    {
        while (!LL_I2C_IsActiveFlag_TXIS(GD_I2C_INST))
        {
        }
        LL_I2C_TransmitData8(GD_I2C_INST, data[i]);
    }
    return 0;
}

uint8_t i2c_read_blocking(uint8_t addr)
{
    uint8_t data[] = {addr};
    i2c_send_blocking(data, 1);
    LL_I2C_HandleTransfer(GD_I2C_INST,
                          GD_ADDRESS,
                          LL_I2C_ADDRSLAVE_7BIT,
                          1,
                          LL_I2C_MODE_AUTOEND,
                          LL_I2C_GENERATE_START_READ);
    while (!LL_I2C_IsActiveFlag_RXNE(GD_I2C_INST))
    {
    }
    return LL_I2C_ReceiveData8(GD_I2C_INST);
}

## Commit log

2022-11-28 Init commit
    [braking_circuitkicad_sch.kicad_sch, can_bus.kicad_sch, mcu.kicad_sch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]
2022-12-01 Move files
    [braking_circuitkicad_sch.kicad_sch, can_bus.kicad_sch, mcu.kicad_sch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]
2022-12-01 Rename KiCad project to `moco-o`
    [moco-o.kicad_pcb, moco-o.kicad_sch]
2022-12-02 Add MoCo-S KiCad project
    [can_bus.kicad_sch, mcu.kicad_sch, moco-s.kicad_pcb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]
2022-12-02 Update net classes
    [moco-s.kicad_pcb]
2022-12-03 Update layout
    [can_bus.kicad_sch, mcu.kicad_sch, moco-s.kicad_pcb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]
2022-12-04 Comp MoCo-S
    [can_bus.kicad_sch, mcu.kicad_sch, moco-s.kicad_pcb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]
2022-12-04 Update sch
    [moco-s.kicad_sch]
2022-12-04 Update ref
    [can_bus.kicad_sch, mcu.kicad_sch, moco-s.kicad_pcb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]
2022-12-06 Use kelvin connection for shunt resistance
    [can_bus.kicad_sch, mcu.kicad_sch, moco-s.kicad_pcb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]
2022-12-06 Replace some extended parts to basic parts
    [can_bus.kicad_sch, mcu.kicad_sch, moco-s.kicad_pcb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]
2022-12-06 Add PCBA files
    [moco-s_BOM.csv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]
2022-12-07 Update doc info
    [moco-s.kicad_pcb, moco-s.kicad_sch]
2022-12-16 Update C47, C48 to the correct part number
    [can_bus.kicad_sch, moco-s.kicad_sch, moco-s_BOM.csv]
2023-01-06 Update LED-G resistor value
    [moco-s.kicad_pcb, moco-s.kicad_sch, moco-s_BOM.csv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]
2023-07-08 Add moco8316 project
    [moco8316.kicad_pcb, moco8316.kicad_sch]
2023-07-08 Move KiCad files to hardware/
    [braking_circuitkicad_sch.kicad_sch, can_bus.kicad_sch, mcu.kicad_sch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]
2023-07-20 Change to DRV8323H
    [braking_circuitkicad_sch.kicad_sch, can_bus.kicad_sch, mcu.kicad_sch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]
2023-07-20 Update edge
    [moco8316.kicad_pcb, moco8316.kicad_sch]
2023-07-20 Add OI451 KiCad project
    [moco-oi451.kicad_pcb, moco-oi451.kicad_sch]
2023-07-21 OI451 routed
    [driver.kicad_sch, mcu.kicad_sch, moco-oi451.kicad_pcb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]
2023-07-21 Reroute and reduce size to Ø40mm
    [driver.kicad_sch, mcu.kicad_sch, moco-oi451.kicad_pcb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]
2023-07-22 Optimize routing
    [driver.kicad_sch, mcu.kicad_sch, moco-oi451.kicad_pcb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]
2023-07-22 Add pcb info
2023-07-22 Add high temperature warning silkscreen
    [moco-oi401.kicad_pcb]
2023-07-22 Update part#
    [driver.kicad_sch, mcu.kicad_sch, moco-oi401.kicad_pcb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]
2023-07-25 BKD8316 routed
    [moco-bkd8316.kicad_pcb, moco-bkd8316.kicad_sch]
2023-07-25 RD401 basic routed
    [can_bus.kicad_sch, moco-rd401.kicad_pcb, moco-rd401.kicad_sch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]
2023-07-25 Remove unused CAN bus schematic
    [can_bus.kicad_sch]
2023-07-25 Rename power stage to triple half bridge
    [triple_half_bridge.kicad_sch]
2023-07-28 Add STSPIN32G4 project
    [moco-pg4.kicad_pcb, moco-pg4.kicad_sch, moco-pg4_2.kicad_pcb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]
2023-07-29 Routed moco-SC1 rev1
    [moco-pg4_2.kicad_pcb, moco-pg4_2.kicad_sch, power_stage.kicad_sch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]
2023-07-30 Update parts
    [moco-sc1.kicad_pcb, moco-sc1.kicad_sch, power_stage.kicad_sch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]
2023-07-30 Remove unused files (moco-pg4_2)
    [moco-pg4_2.kicad_pcb, moco-pg4_2.kicad_sch, power_stage.kicad_sch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]
2023-07-30 Change to 4 layers board
    [moco-sc1.kicad_pcb, moco-sc1.kicad_sch]
2023-07-30 Update connector
2023-07-30 Update board characteristics
2023-08-08 Fix the bug of params
    [main.cpp]
2024-01-14 Update license
    [moco-bkd8316.kicad_pcb, moco-oi401.kicad_pcb, moco-oi401.kicad_sch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]
2024-03-26 Add moco-rc1 KiCad Project
    [can_bus.kicad_sch, moco-rc1.kicad_pcb, moco-rc1.kicad_sch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]
2024-03-30 Fix SVPWM (fabs())
    [moco-rc1.kicad_pcb]
2024-05-18 Modify MX config, enable TIM1_CH4 TRGO as current sensing ADC trigger, and enable current sending ADC
2024-05-18 Add ADC injection conversion

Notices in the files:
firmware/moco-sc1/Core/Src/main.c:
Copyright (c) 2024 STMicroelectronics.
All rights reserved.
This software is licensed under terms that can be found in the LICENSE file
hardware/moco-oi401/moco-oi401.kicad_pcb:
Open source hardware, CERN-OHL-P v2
